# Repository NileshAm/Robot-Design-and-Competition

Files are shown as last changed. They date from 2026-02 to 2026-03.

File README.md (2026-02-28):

# Robot Design and Competition
This is the project repository for module EN2533-Robot Design and Competition.</br>
This repository contains all the [design](/Design/) files and [firmware](/Code/) for for the robot we designed.

## Final product

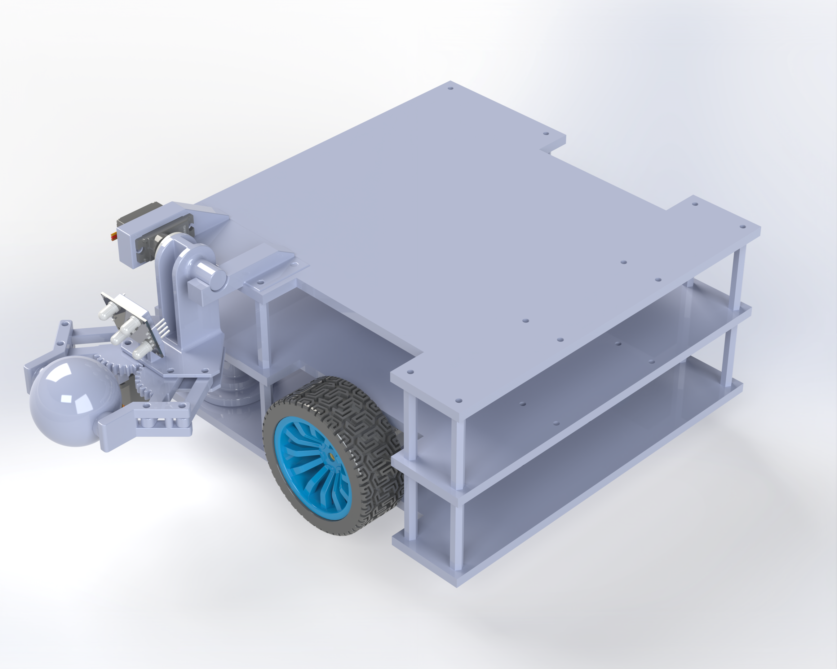
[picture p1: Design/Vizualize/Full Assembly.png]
Robot Image


<p align="center">
  
  
</p>

### Component Selection
| Category | Component | Model / Specification | Quantity | Reason for Selection |
|---|---|---|---|---|
| Controller | Microcontroller | Arduino Mega 2560 | 1 | Mainly choosen for its high pin count to handle the sensors |
| Motor Driver | Motor Driver Module | bts7960 motor driver | 2 | Provides bidirectional control and sufficient current for DC motors |
| Actuator | JGA25-370 12V with encoders | 12V, 280 RPM | 2 | High torque suitable and encoder for precision control of the  robot |
| Battery | 11.1V LiPo |  4800mah | 1 | Lightweight with high energy density |
| Power Regulation | Voltage Regulator | Buck Converter (LM2596),  | 2 | Steps down battery voltage safely for electronics (2 is used for a electronics rail and a high power rail seperated for electronics stability.) |
| Power Regulation | Voltage Regulator | 12V Buck Boost converter,  | 1 | To regulate the motor voltage to be at constant 12V. |
| Sensor | Distance Sensor | VL53LOX Tof Sensors | 5 | Obstacle detection |
| Sensor | Line Sensor | IR Reflective Sensor | 8 | Line-following capability |
| Mechanical | Chassis | 3D Printed | 1 | Strong, lightweight, and custom-fit |
| Mechanical | Wheel | Rubber Wheel (65 mm) | 4 | Good traction and stability |
| Interface | Display | OLED | 1 | System status and debugging feedback |
| Safety | Switch | Toggle / Push Button | 1 | Safe power isolation |

## Folder structure

- [Design](/Design/) : Contains all the robot design files
  - [Parts](/Design/Parts/) : Contains all part files of the design.
  - [Assemblies](/Design/Assemblies/) : Contains all the assembly files.
  - [Drawings](/Design/Drawings/) : Contains all the enginnering drawing files.
  - [Manufacturing](/Design/Manufacturing/) : Contains all the files required to manufacture the robot.

- [Code](/Code/) : Contains all the firmware for the robot.
  - [include](/Code/include/) : Project headers for files. ([/include/README.md](/Code/include/README.md))
  - [lib](/Code/lib/) : Project specific component files. ([/lib/README.md](/Code/lib/README.md))
  - [src](/Code/src/) : Main file of the project.
  - [test](/Code/test/) : Test files of the project. ([/test/README.md](/Code/test/README.md))

## Branching Structure

- **Main Branch** : All the design and firmware files.
- **Design branch** : Changes made to the design of the robot is done here
  - **Design sub-branch** : Individual changes of the desgin of the robot are done in these braches.<br>
    - Name must follow the convention : `design-*`<br>
      - Example : `design-arm`

    - After finishing the sub-branch design, branch must be merged with the **Design branch** with and the with the **Main branch**.
  - **Code sub-branch** : Individual changes of firmware of the robot are done in these braches.<br>
    - Name must follow the convention : `code-*`<br>
      - Example : `code-PID`

    - After finishing the sub-branch, branch must be merged with the **Code branch** with and the with the **Main branch**.

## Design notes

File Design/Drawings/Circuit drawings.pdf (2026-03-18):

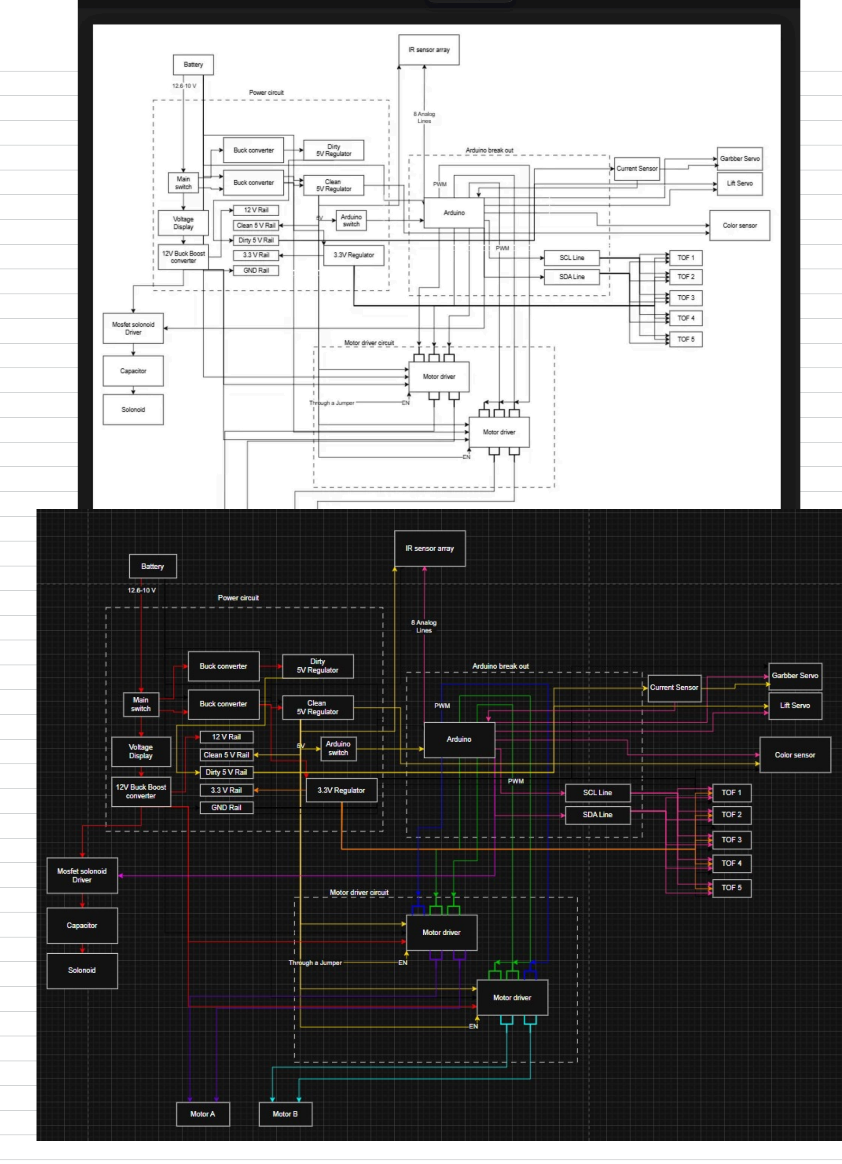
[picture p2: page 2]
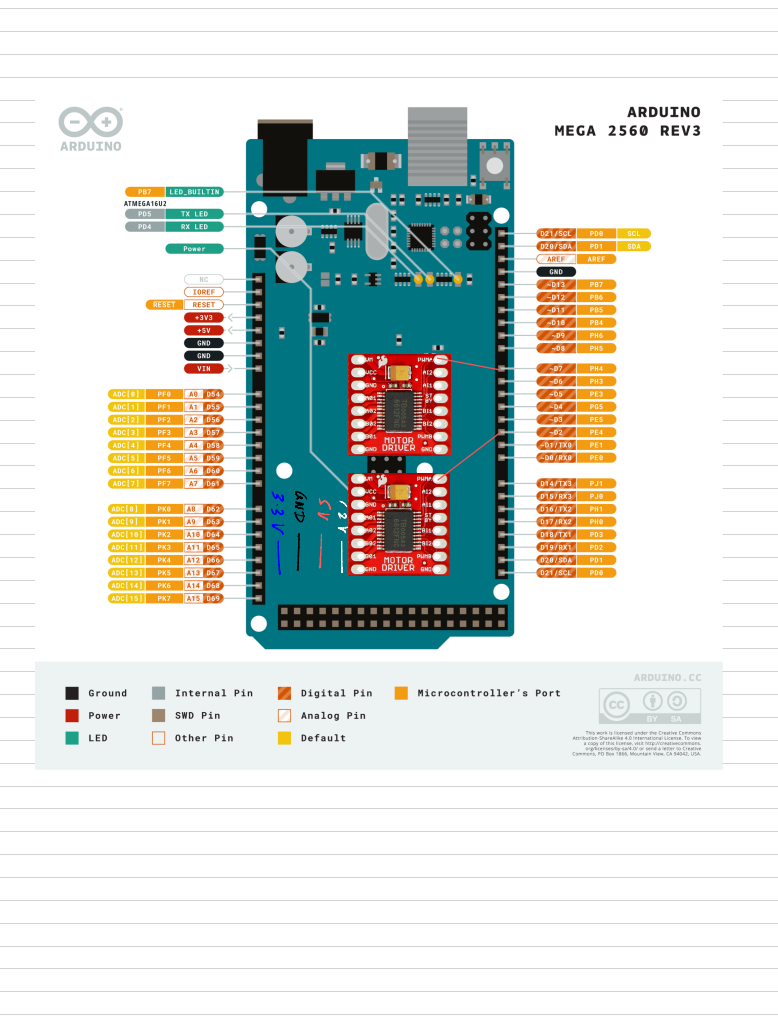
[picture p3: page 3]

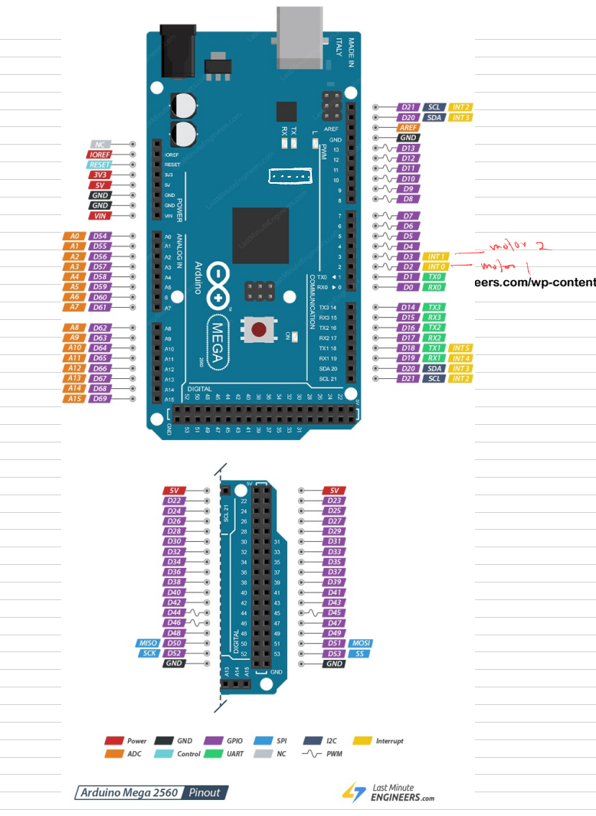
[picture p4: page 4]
motor 2; motor (

https://lastminuteengineers.com/wp-content/uploads/arduino/Arduino-Mega-2560-Pinout.png

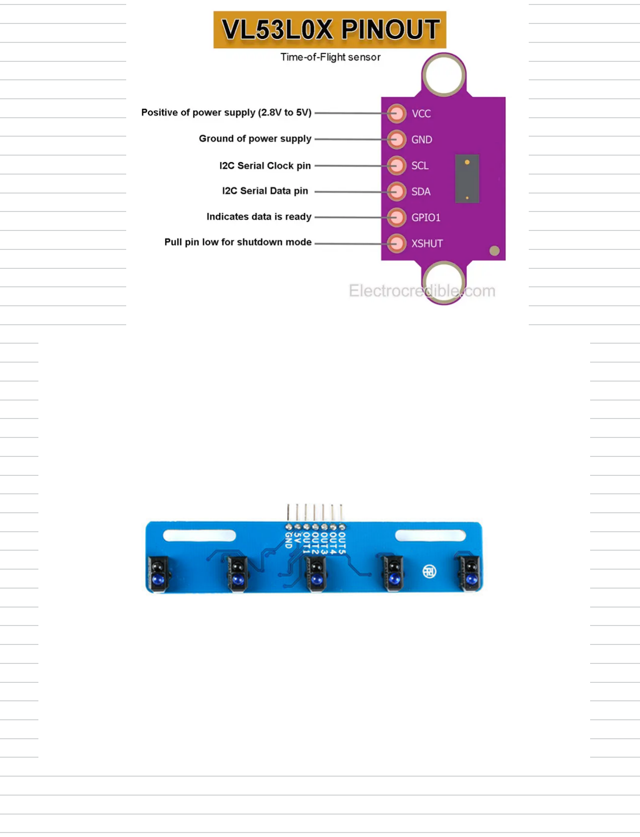
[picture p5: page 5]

https://www.google.com/url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

https://content.instructables.com/FCN/O9VG/JHATTMWR/FCNO9VGJHATTMWR.png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.

https://www.google.com/url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

# aut

↳

motor powere

,

⑧ | -S

2

C

# motor power

# =>inteaua digital

E

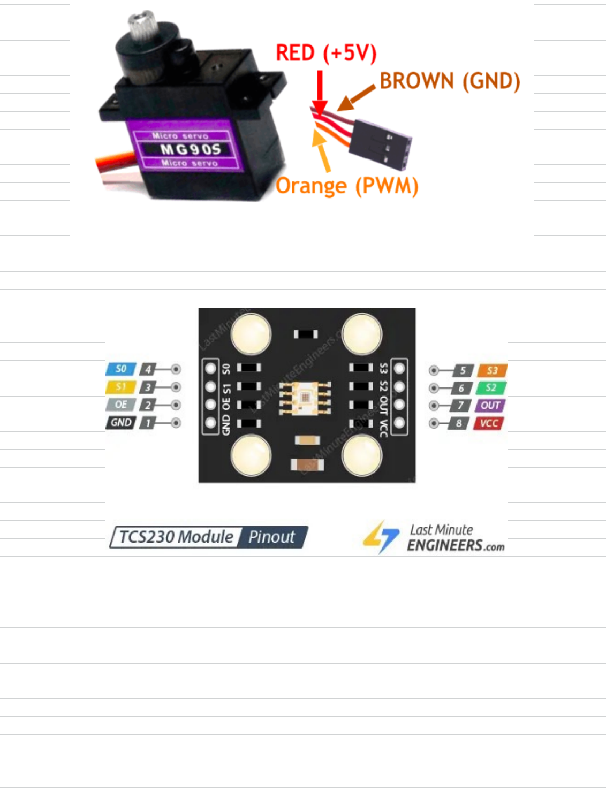
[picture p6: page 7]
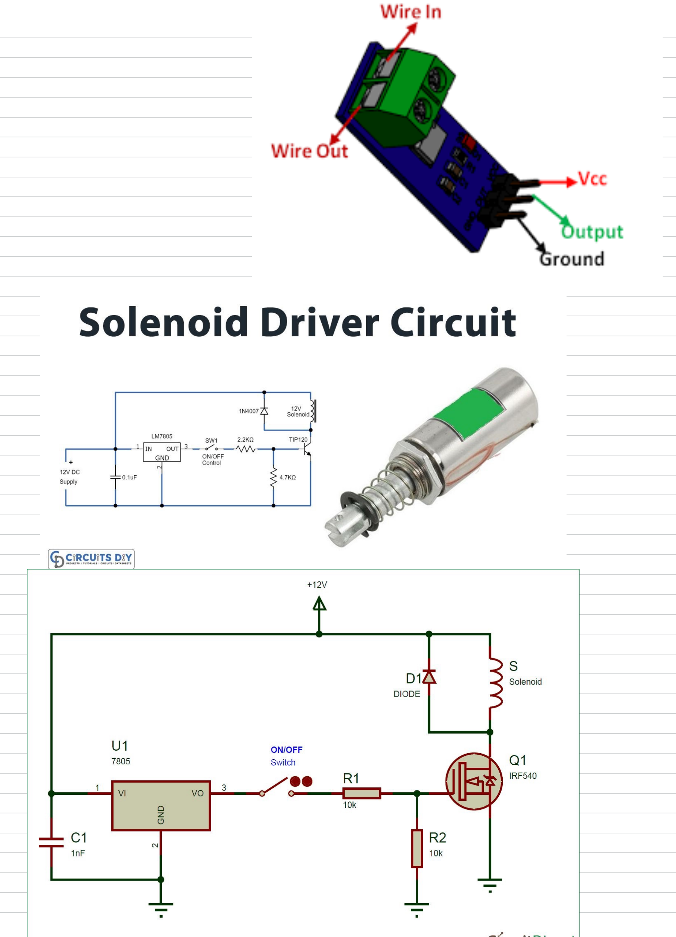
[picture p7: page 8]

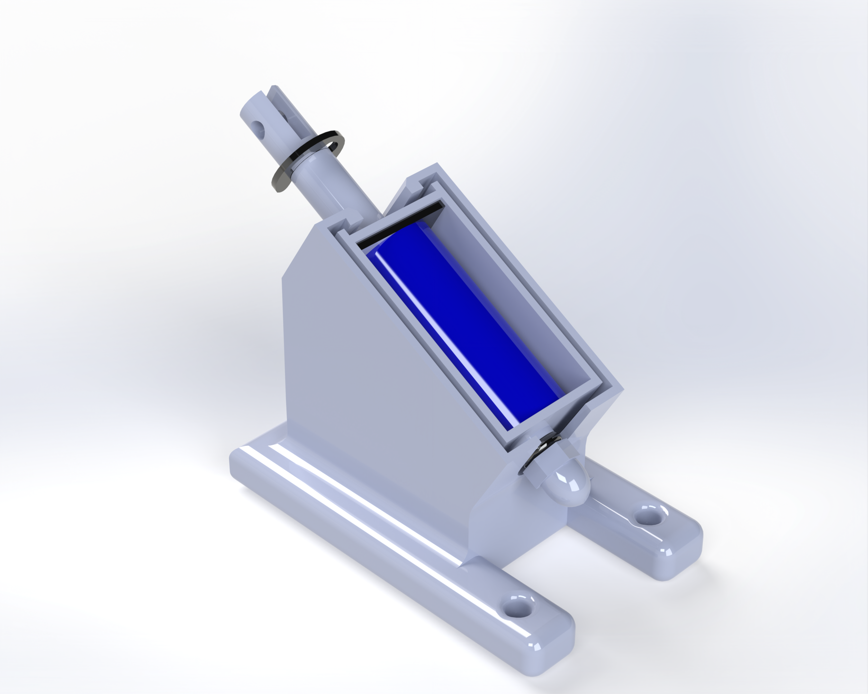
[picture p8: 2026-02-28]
Design/Vizualize/Solenoid.png

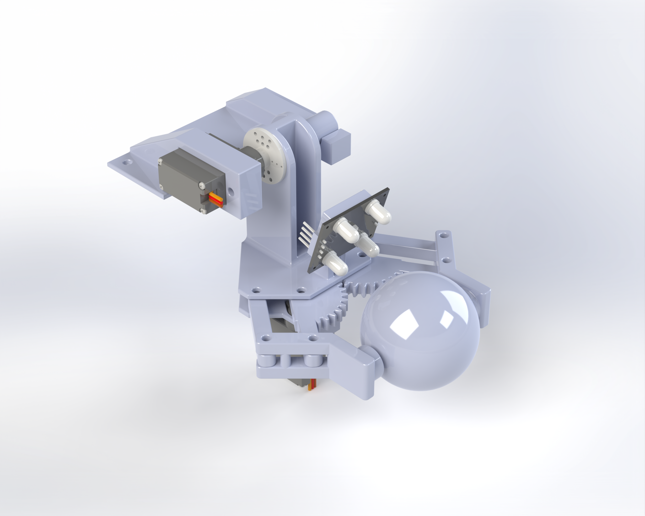
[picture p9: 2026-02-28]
Design/Vizualize/Grabber.png

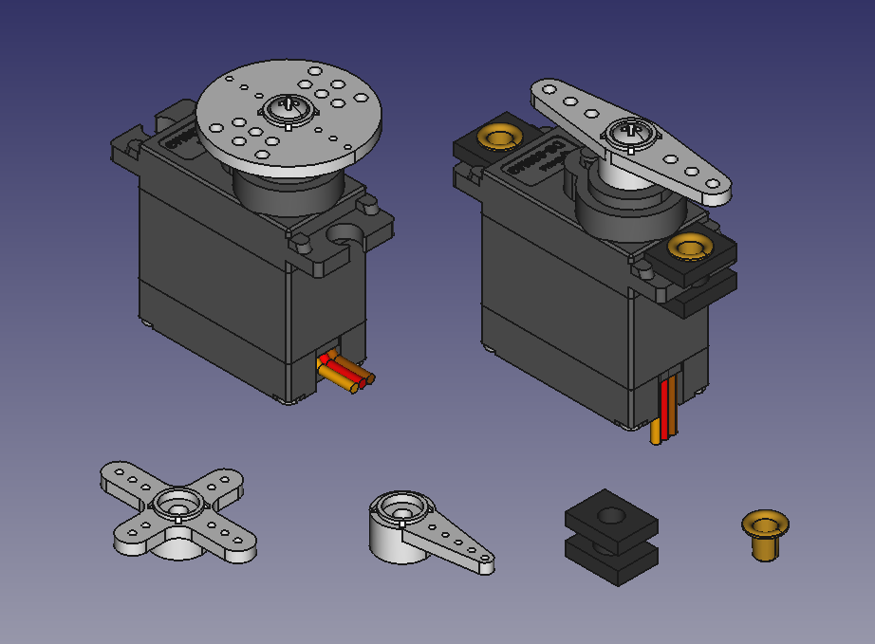
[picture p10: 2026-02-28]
Design/Downloads/digital-servo-corona-ds-939mg-with-accessories-1.snapshot.11/Corona_DS939MG_Set.png

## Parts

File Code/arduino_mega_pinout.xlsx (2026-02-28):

Pin_Name | Pin_Number | Type | PWM | UART | I2C | SPI | Interrupt | Onboard_Feature | Usage Type | Usage
D0 | 0 | Digital I/O | No | RX0 (Serial0) |  |  | No
D1 | 1 | Digital I/O | No | TX0 (Serial0) |  |  | No
D2 | 2 | Digital I/O | Yes |  |  |  | Yes |  | Right Motor | encA
D3 | 3 | Digital I/O | Yes |  |  |  | Yes |  | Left Motor | encA
D4 | 4 | Digital I/O | Yes |  |  |  | No |  | Right Motor | PWM backward
D5 | 5 | Digital I/O | Yes |  |  |  | No |  | Right Motor | PWM forward
D6 | 6 | Digital I/O | Yes |  |  |  | No |  | Right Motor | PWM forward
D7 | 7 | Digital I/O | Yes |  |  |  | No |  | Right Motor | PWM backward
D8 | 8 | Digital I/O | Yes |  |  |  | No |  | Servo | Grabber
D9 | 9 | Digital I/O | Yes |  |  |  | No |  | Servo | Lift
D10 | 10 | Digital I/O | Yes |  |  |  | No
D11 | 11 | Digital I/O | Yes |  |  |  | No
D12 | 12 | Digital I/O | Yes |  |  |  | No
D13 | 13 | Digital I/O | Yes |  |  |  | No | On-board LED (L)
D14 | 14 | Digital I/O | No | TX3 (Serial3) |  |  | No
D15 | 15 | Digital I/O | No | RX3 (Serial3) |  |  | No
D16 | 16 | Digital I/O | No | TX2 (Serial2) |  |  | No
D17 | 17 | Digital I/O | No | RX2 (Serial2) |  |  | No
D18 | 18 | Digital I/O | No | TX1 (Serial1) |  |  | Yes
D19 | 19 | Digital I/O | No | RX1 (Serial1) |  |  | Yes
D20 | 20 | Digital I/O | No |  | SDA (I2C) |  | Yes |  | I2C | SDA
D21 | 21 | Digital I/O | No |  | SCL (I2C) |  | Yes |  | I2C | SCL
D22 | 22 | Digital I/O | No |  |  |  | No |  | Right Motor | encB
D23 | 23 | Digital I/O | No |  |  |  | No |  | IR | IR
D24 | 24 | Digital I/O | No |  |  |  | No |  | Left Motor | encB
D25 | 25 | Digital I/O | No |  |  |  | No |  | IR | IR
D26 | 26 | Digital I/O | No |  |  |  | No
D27 | 27 | Digital I/O | No |  |  |  | No |  | IR | IR
D28 | 28 | Digital I/O | No |  |  |  | No |  | Right Motor | dir1
D29 | 29 | Digital I/O | No |  |  |  | No |  | IR | IR
D30 | 30 | Digital I/O | No |  |  |  | No |  | Right Motor | dir2
D31 | 31 | Digital I/O | No |  |  |  | No |  | IR | IR
D32 | 32 | Digital I/O | No |  |  |  | No |  | Left Motor | dir1
D33 | 33 | Digital I/O | No |  |  |  | No |  | IR | IR
D34 | 34 | Digital I/O | No |  |  |  | No |  | Left Motor | dir2
D35 | 35 | Digital I/O | No |  |  |  | No |  | IR | IR
D36 | 36 | Digital I/O | No |  |  |  | No |  | Tof | Right Tof
D37 | 37 | Digital I/O | No |  |  |  | No |  | IR | IR
D38 | 38 | Digital I/O | No |  |  |  | No |  | Tof | Front Top Tof
D39 | 39 | Digital I/O | No |  |  |  | No
D40 | 40 | Digital I/O | No |  |  |  | No |  | Tof | Front TOF
D41 | 41 | Digital I/O | No |  |  |  | No
D42 | 42 | Digital I/O | No |  |  |  | No |  | Tof | Left Tof 2
D43 | 43 | Digital I/O | No |  |  |  | No |  | Grabber Color | S0
D44 | 44 | Digital I/O | Yes |  |  |  | No |  | Tof | Left Tof
D45 | 45 | Digital I/O | Yes |  |  |  | No |  | Grabber Color | S1
D46 | 46 | Digital I/O | Yes |  |  |  | No
D47 | 47 | Digital I/O | No |  |  |  | No |  | Grabber Color | S2
D48 | 48 | Digital I/O | No |  |  |  | No |  | Button | Down Button
D49 | 49 | Digital I/O | No |  |  |  | No |  | Grabber Color | S3
D50 | 50 | Digital I/O | No |  |  | MISO (SPI) | No |  | Button | Up Button
D51 | 51 | Digital I/O | No |  |  | MOSI (SPI) | No |  | Grabber Color | out
D52 | 52 | Digital I/O | No |  |  | SCK (SPI) | No |  | Button | Select Button
D53 | 53 | Digital I/O | No |  |  | SS (SPI) | No |  | Grabber Color | OE
A0 | 54 | Analog Input / Digital I/O | No |  |  |  | No |  | Box Color | S0
A1 | 55 | Analog Input / Digital I/O | No |  |  |  | No |  | Box Color | S1
A2 | 56 | Analog Input / Digital I/O | No |  |  |  | No |  | Box Color | S2
A3 | 57 | Analog Input / Digital I/O | No |  |  |  | No |  | Box Color | S3
A4 | 58 | Analog Input / Digital I/O | No |  |  |  | No |  | Box Color | out
A5 | 59 | Analog Input / Digital I/O | No |  |  |  | No |  | Box Color | OE
A6 | 60 | Analog Input / Digital I/O | No |  |  |  | No
A7 | 61 | Analog Input / Digital I/O | No |  |  |  | No
A8 | 62 | Analog Input / Digital I/O | No |  |  |  | No |  | Currect sensor | Currect sensor
A9 | 63 | Analog Input / Digital I/O | No |  |  |  | No
A10 | 64 | Analog Input / Digital I/O | No |  |  |  | No
A11 | 65 | Analog Input / Digital I/O | No |  |  |  | No
A12 | 66 | Analog Input / Digital I/O | No |  |  |  | No
A13 | 67 | Analog Input / Digital I/O | No |  |  |  | No
A14 | 68 | Analog Input / Digital I/O | No |  |  |  | No
A15 | 69 | Analog Input / Digital I/O | No |  |  |  | No
IOREF |  | Power/Ref
RESET |  | Reset
3.3V |  | Power
5V |  | Power
GND |  | Ground
GND |  | Ground
VIN |  | Power Input
AREF |  | Analog Reference
GND |  | Ground
GND |  | Ground
SDA | 20 | I2C Header |  |  | SDA (I2C, same as D20)
SCL | 21 | I2C Header |  |  | SCL (I2C, same as D21)
ICSP_MISO | 50 | SPI (ICSP) |  |  |  | MISO (SPI, same as D50)
ICSP_MOSI | 51 | SPI (ICSP) |  |  |  | MOSI (SPI, same as D51)
ICSP_SCK | 52 | SPI (ICSP) |  |  |  | SCK (SPI, same as D52)
ICSP_RESET |  | Reset (ICSP)
ICSP_VCC |  | Power (ICSP)
ICSP_GND |  | Ground (ICSP)

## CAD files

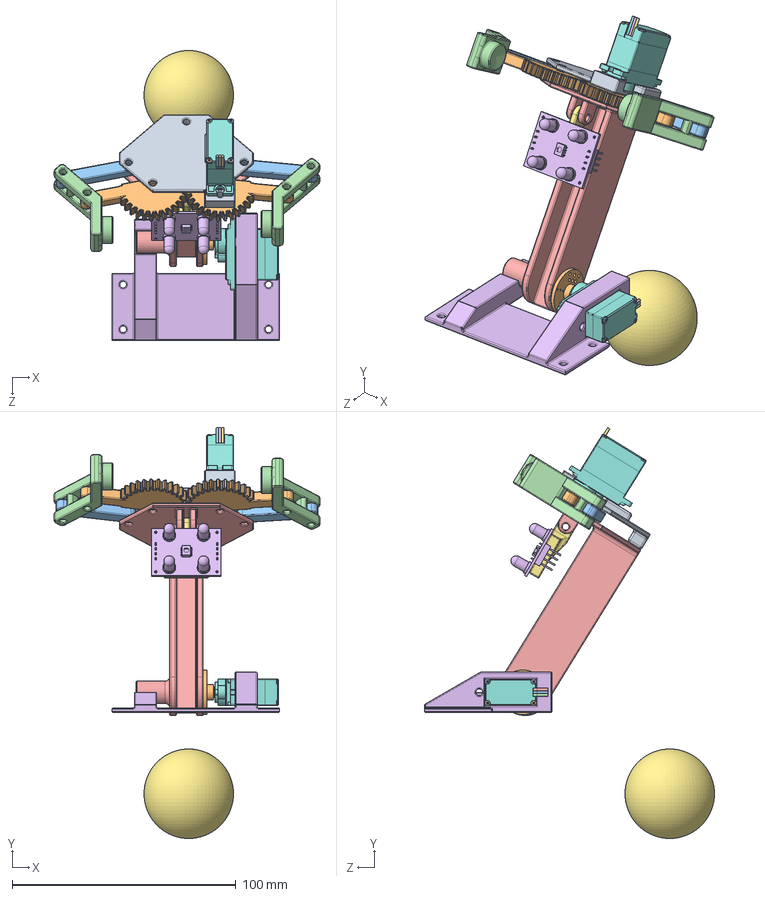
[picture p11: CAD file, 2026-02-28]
Design/Assemblies/Grabber.SLDASM
118.7 x 183.7 x 129.6 mm
Grabber base bottom
Link front x 2
Link back x 2
Grabbing link x 2
Grabber base top
TCS230-TCS3200
Color sensor mount
Corps.step x 2
M1.2-Screw001.step x 2
M1.2-Screw002.step x 2
M1.2-Screw003.step x 2
M1.2-Screw004.step x 2
Axe.step x 2
FilRougeDroit.step
FilMarronDroit.step
FilOraqngeDroit.step
Etiquette2.step x 2
Corona_DS939MG-BrasRond.step
FilRougeCoude.step
FilMarronCoude001.step
FilOrangeCoude002.step
Lift servo mount
Ball

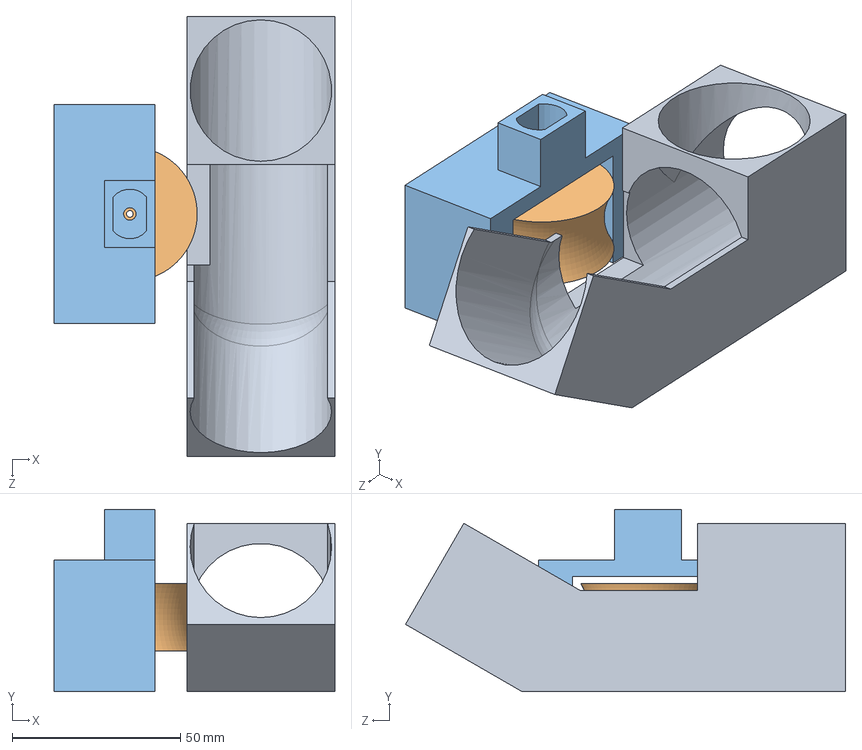
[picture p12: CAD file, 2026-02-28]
Design/Assemblies/Shooter.SLDASM
83.4 x 54.1 x 130.6 mm
Ramp
Fly wheel
Fly wheel motor mount

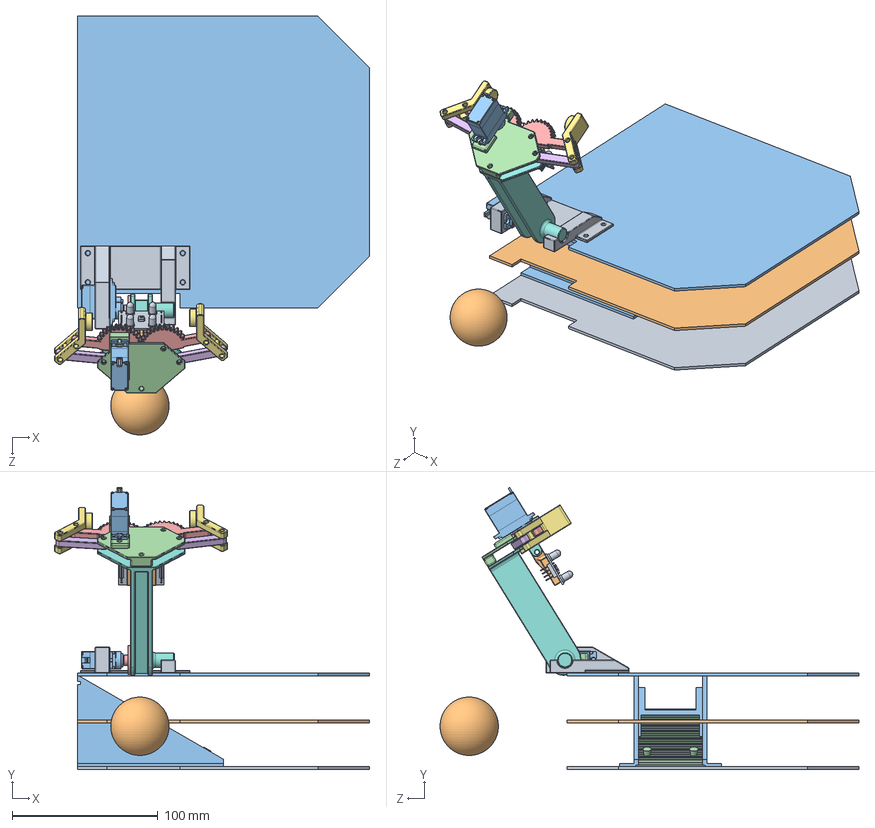
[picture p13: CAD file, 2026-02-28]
Design/Assemblies/Robot.SLDASM
215.9 x 193.3 x 287.1 mm
Base level
Level 2
Level 3
Grabber base bottom
Link front x 2
Link back x 2
Grabbing link x 2
Grabber base top
TCS230-TCS3200
Color sensor mount
Corps.step x 2
M1.2-Screw001.step x 2
M1.2-Screw002.step x 2
M1.2-Screw003.step x 2
M1.2-Screw004.step x 2
Axe.step x 2
FilRougeDroit.step
FilMarronDroit.step
FilOraqngeDroit.step
Etiquette2.step x 2
Corona_DS939MG-BrasRond.step
FilRougeCoude.step
FilMarronCoude001.step
FilOrangeCoude002.step
Lift servo mount
Ball
Slider base
Rack

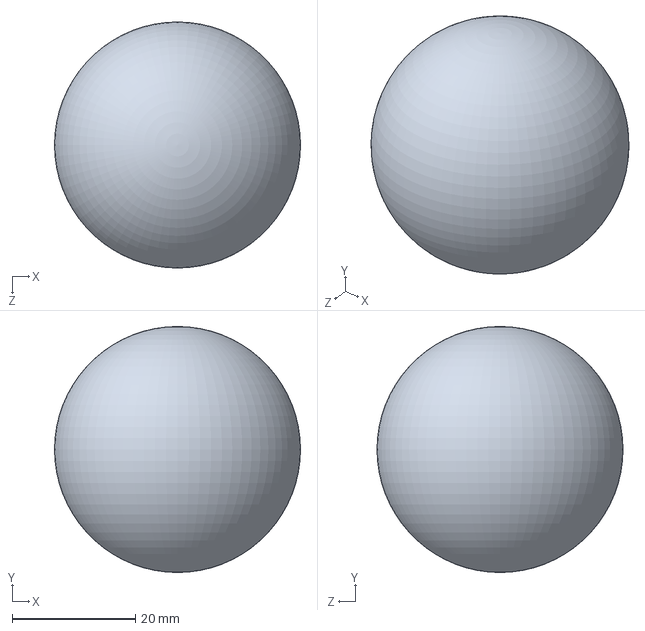
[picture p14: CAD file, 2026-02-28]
Design/Arena/Ball.SLDPRT
40.0 x 40.0 x 40.0 mm

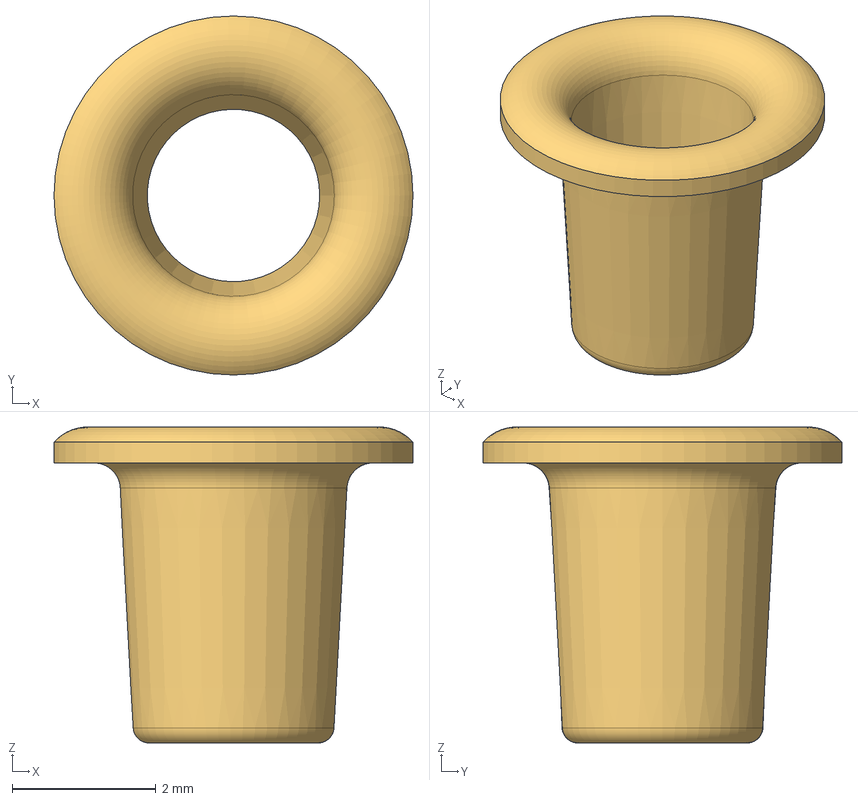
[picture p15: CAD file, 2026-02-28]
Design/Downloads/digital-servo-corona-ds-939mg-with-accessories-1.snapshot.11/Corona_DS939MG_Accessoires.FCStd
5.00 x 5.00 x 4.40 mm

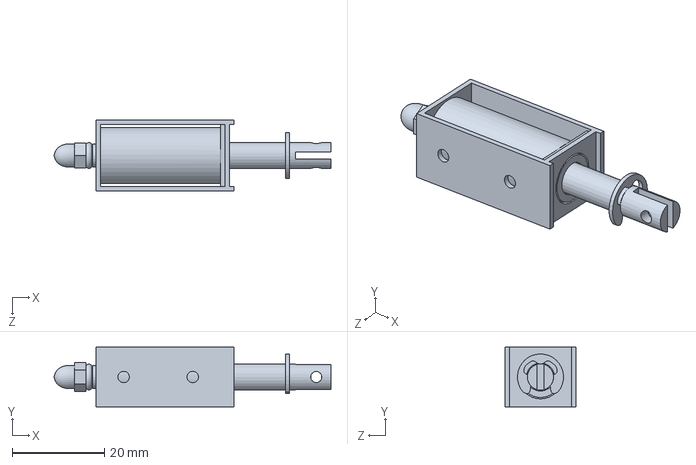
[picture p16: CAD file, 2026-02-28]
Design/Downloads/JF-0530B Selenoid itme çekme valfi.SLDPRT
60.1 x 13.0 x 15.5 mm

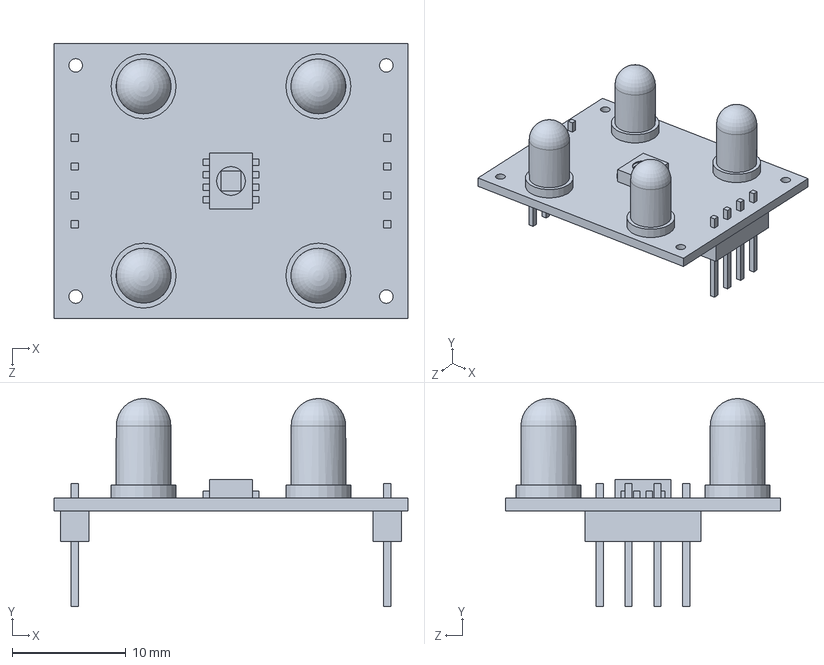
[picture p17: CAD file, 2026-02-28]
Design/Downloads/tcs230-tcs3200-1.snapshot.1/TCS230-TCS3200.SLDPRT
31.1 x 18.3 x 24.1 mm

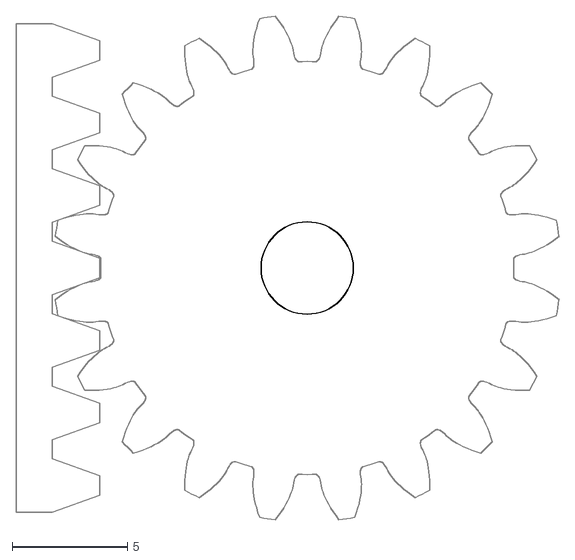
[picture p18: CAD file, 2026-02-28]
Design/Gears/Rack and pinion.dxf
23.5 x 21.8

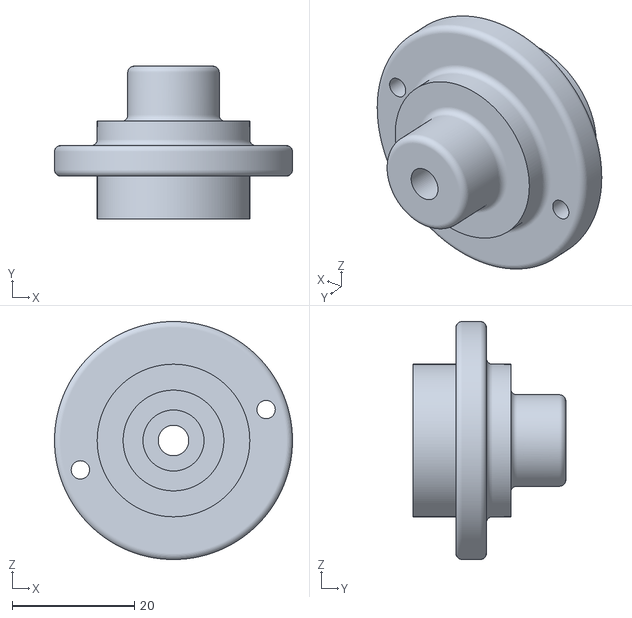
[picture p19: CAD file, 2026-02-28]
Design/Manufacturing/Ball Bearim 3_V0.2.STL
39.0 x 25.0 x 39.0

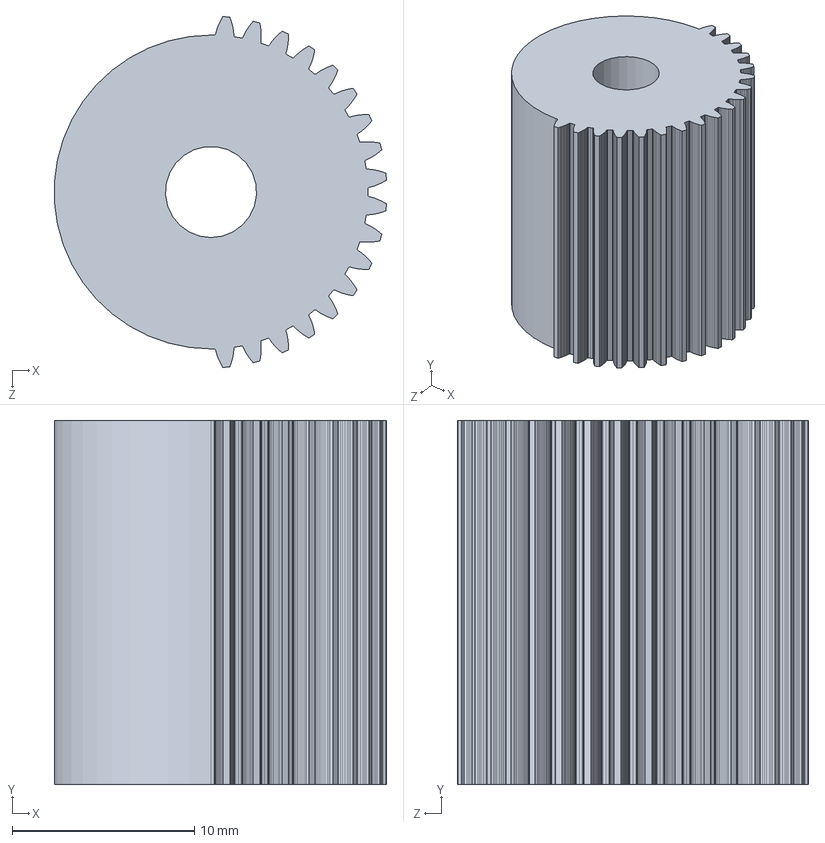
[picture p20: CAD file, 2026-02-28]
Design/Parts/Gear_new_1.SLDPRT
18.2 x 20.0 x 19.3 mm

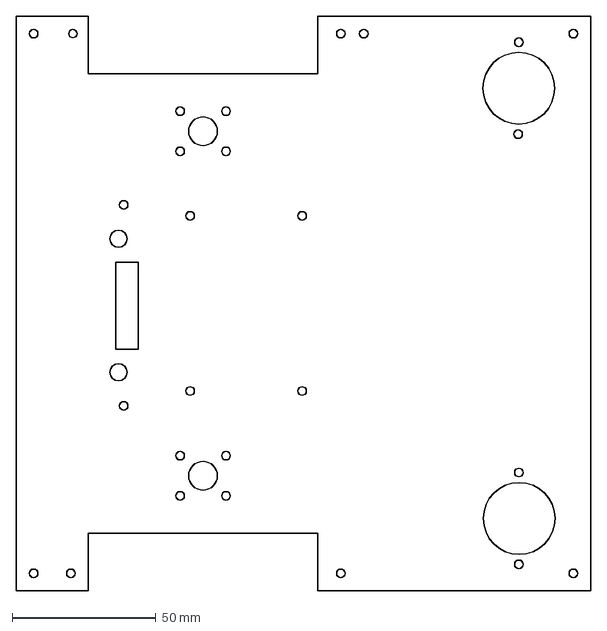
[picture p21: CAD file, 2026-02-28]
Design/Drawings/Chasis 01_V0.3.DXF
200.0 x 200.0 mm

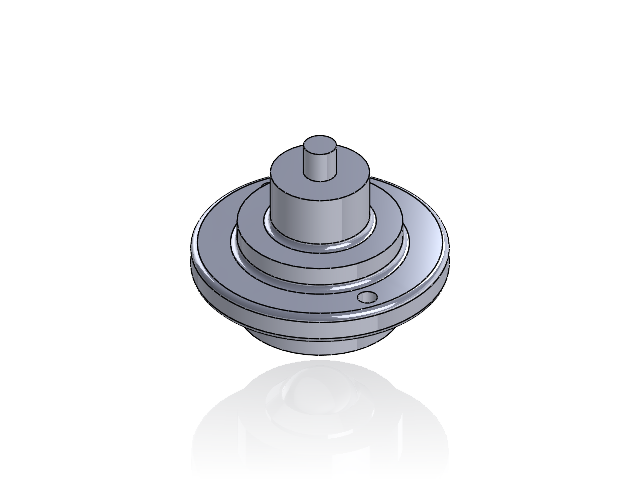
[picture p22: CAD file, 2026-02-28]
Assmblies/Ball Bearim_Assembly_with_mount.SLDASM
Ball Bearim 1
Ball Bearim 2
Ball Bearim 3_V0.2

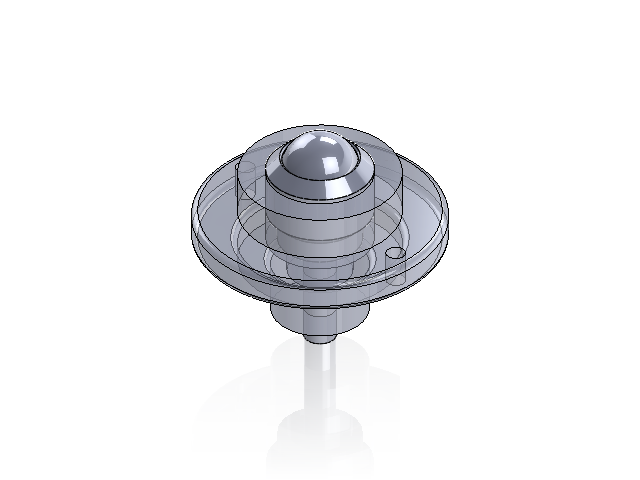
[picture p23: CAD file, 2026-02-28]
Assmblies/Ball Bearim.SLDASM
Ball Bearim 1
Ball Bearim 2
Ball Bearim 3_V0.2

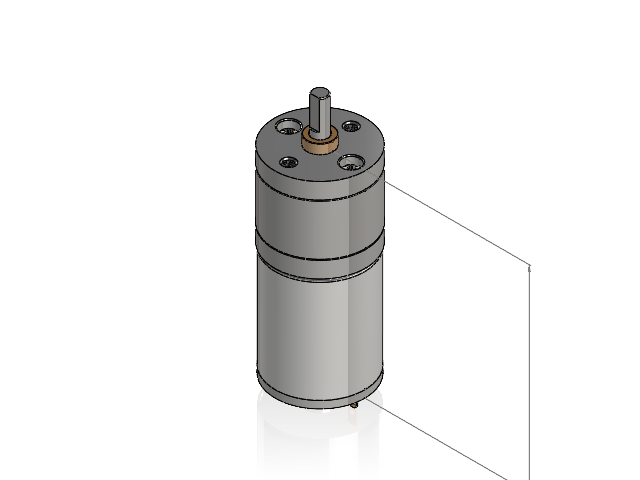
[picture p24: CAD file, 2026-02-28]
Design/Downloads/JGA25-370.SLDASM
Motor.step
Gearbox.step
90116A027_316 Stainless Steel Pan Head Phillips Screws.step x 2

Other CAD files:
Assmblies/IE ARRAY.SLDASM
Assmblies/Solenoid_Assembly.SLDASM
Assmblies/Shooter_Assembly_V0.2.SLDASM
Design/Downloads/digital-servo-corona-ds-939mg-with-accessories-1.snapshot.11/Corona_DS939MG_Fixing.step
Design/Downloads/SG90-servo.SLDPRT
Design/Downloads/digital-servo-corona-ds-939mg-with-accessories-1.snapshot.11/Corona_DS939MG-BrasCroix.step
Design/Downloads/digital-servo-corona-ds-939mg-with-accessories-1.snapshot.11/Corona_DS939MG-BrasDouble.step
Design/Downloads/digital-servo-corona-ds-939mg-with-accessories-1.snapshot.11/Corona_DS939MG-BrasRond.step
Design/Downloads/digital-servo-corona-ds-939mg-with-accessories-1.snapshot.11/Corona_DS939MG-BrasSimple.step
Design/Downloads/digital-servo-corona-ds-939mg-with-accessories-1.snapshot.11/Corona_DS939MG_ShockAbsorber.step
Design/Downloads/mounting_motor.SLDPRT
Design/Drawings/Chasis 01_V0.1.DXF
Design/Drawings/Chasis 02_V0.2.DXF
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

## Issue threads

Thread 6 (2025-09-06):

Color sensor helper

NileshAm, 2025-09-06:
### Make a color sensor helper library
- Library file must be made using a **class**. Refer [PID](https://github.com/NileshAm/Robot-Design-and-Competition/tree/code-init/Code/lib/PID) for example of an implemented code.

- [ ] Make the ColorSensor.h file
- [ ] Make the ColorSensor.cpp file
- [ ] Make examples.cpp file in `/examples` folder and write a basic implementation sketch.
- [ ] Implement `isRed()`, `isBlue()`, `isGreen()` , `isBlack()`, `isWhite()` methods.
- [ ] Implement `calibrate()` method.

NileshAm, 2025-09-24:
Completed with 18c24d7ac931fc67b3842cd5ee2de3503973ed4a commit.

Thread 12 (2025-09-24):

User menu

NileshAm, 2025-09-24:
## Menu implementation
Implementing the menu that controls the robot.

Implementation strategy for the menu is **_not finalized_**.

- [ ] Implement a menu that shows the items. Menu should be as follows.
```python
* Run All  // * marks the current selection
  Calibrate
  Run task 1
  .
  .
  .
```

- [ ] 2 buttons must be configured to go up and down the menu.
- [ ] 1 interrupt button must be configured.
  - To stop the current task if a task is running and open the menu.
  - To select the selected(the menu item where the `*` is current located)
- [ ] Apon selection method should return a value (Preferably a `int`), to be used in a switch case to put the robot in each state.

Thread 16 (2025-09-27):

Grabber helper

NileshAm, 2025-09-27:
## Grabber helper

Features to be implemented

- [ ] `Grabber` class with constructor.
- [ ] constructor must take 2 servo motors, current sensor and grabber tof as parameters and initialize them.
- [ ] `grab` method must turn the servo till current spike is detected and grab the object.
- [ ] `lift` method must lift the arm from initial position to the release position.
- [ ] `relaese` method must open the grabbers fully.
- [ ] `reset` method must bring down the arm and make the grabber ready to grab the next object.

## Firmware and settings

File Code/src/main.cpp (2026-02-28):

#include <Arduino.h>
#include <Motor.h>
#include <IRArray.h>
#include <Tof.h>
#include <OLED.h>
#include <ColorSensor.h>
#include <Grabber.h>
#include <ServoMotor.h>
#include <CurrentSensor.h>
#include <Robot.h>
#include <Utils.h>
#include <pushbutton.h>
#include <MenuSystem.h>
#include <UpdatePID.h>
#include <ServoMotor.h>
#include <MPU6050.h>

void setup()
{
    Serial.begin(9600);
    Serial.println("Setup started...");
    

    OLED oled;
    oled.begin();
    oled.displayText("Initializing...", 0, 0, 1);
    Serial.println("Initializing...");

    Motor leftMotor(28, 30, 4, 5, 2, 22, 450); // dir1, dir2, pwmF, pwmB, encA, encB, ticks/rev     motor controller 1
    Motor rightMotor(32, 34, 7, 6, 3, 24, 450);  // dir1, dir2, pwmF, pwmB, encA, encB, ticks/rev   motor controller 2
    leftMotor.init();
    rightMotor.init();
    oled.displayText("Motor init complete...", 0, 10, 1);
    
    const uint8_t PINS[8] = {23, 25, 27, 29, 31, 33, 35, 37};
    // equal weights (or set your own)
    const float W[8] = {0, 100, 200, 300, 400, 500, 600, 700};
    IRArray ir(8, PINS, W, 0.5f);
    ir.init();
    oled.displayText("IR init complete...", 0, 20, 1);

    Tof frontTof(40, 0x30, 20, 21);    // xshut, address, sda, scl
    Tof leftTof(44, 0x31, 20, 21);     // xshut, address, sda, scl
    Tof leftTof2(42, 0x34, 20, 21);    // xshut, address, sda, scl
    Tof rightTof(36, 0x32, 20, 21);    // xshut, address, sda, scl
    Tof frontTopTof(38, 0x33, 20, 21); // xshut, address, sda, scl

    frontTof.disable();
    leftTof.disable();
    leftTof2.disable();
    rightTof.disable();
    frontTopTof.disable();

    frontTof.init(25);
    leftTof.init(20);
    leftTof2.init(-8);
    rightTof.init(17);
    frontTopTof.init(48);

    ColorSensor boxColorSensor(A0, A1, A2, A3, A4, A5);
    ColorSensor grabberSensor(43, 45, 47, 49, 51, 53);
    boxColorSensor.begin();
    grabberSensor.begin();
    oled.displayText("Color init complete...", 0, 40, 1);
    
    pushbutton btnUp(50);
    pushbutton btnDown(48);
    pushbutton btnSelect(52);
    btnUp.init();
    btnDown.init();
    btnSelect.init();
    oled.clear();
    oled.displayText("Button init complete...", 0, 0, 1); 
    
    // --- Grabber Initialization ---
    ServoMotor grabServo(8); 
    ServoMotor liftServo(9);
    CurrentSensor currentSensor(A8, 0.001, 60); 
    Grabber grabber(grabServo, liftServo, currentSensor);
    grabber.init();
    
    MPU6050 imu = MPU6050();
    imu.begin();
    oled.displayText("IMU init complete...", 0, 10, 1);

    Robot robot(rightMotor, leftMotor, ir, frontTof, leftTof, leftTof2, frontTopTof, rightTof, grabberSensor, boxColorSensor, grabber, oled, imu);
    oled.displayText("Robot init complete...", 0, 10, 1);


    oled.clear();
    MenuSystem *menu;
    menu = new MenuSystem(oled, btnUp, btnDown, btnSelect, grabberSensor, robot);

    // Initialize Menu
    menu->begin();
    while (true)
    {
        menu->update();
        delay(10);
    }

}

void loop()
{
    // Empty because we have a while(true) in setup,
    // but typically we should move the while(true) content here.
    // For now, keeping it in setup to match existing style,
    // but the while(true) above handles the loop.
}

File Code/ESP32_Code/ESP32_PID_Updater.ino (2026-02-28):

#include <WiFi.h>
#include <WebServer.h>
#include <Preferences.h>

// ---- CONFIGURATION ----
const char* ssid = "Robot_PID_Tuner";  // AP Name
const char* password = "password123";  // AP Password

// Pin connected to Arduino RESET pin
#define ARDUINO_RESET_PIN 4 

// UART to Arduino (Serial2)
#define RXD2 16
#define TXD2 17

Preferences preferences;
WebServer server(80);

// PID Values Structure
struct PIDValues {
  float kp;
  float ki;
  float kd;
};

PIDValues linePID = {0.25, 0.0, 70.0};
PIDValues wallPID = {0.25, 0.1, 90.0};
PIDValues straightPID = {1.5, 1.0, -0.25};

// HTML Page
void handleRoot() {
  String html = R"rawliteral(
<!DOCTYPE HTML><html>
<head>
  <title>PID Tuner</title>
  <meta name="viewport" content="width=device-width, initial-scale=1">
  <style>
    body { font-family: Arial; text-align: center; margin: 0px auto; padding-top: 30px; }
    input, select { padding: 10px; font-size: 20px; width: 80%; max-width: 300px; margin: 10px; }
    input[type=submit] { background-color: #4CAF50; border: none; color: white; padding: 16px 32px; text-decoration: none; margin: 4px 2px; cursor: pointer; font-size: 20px;}
    .label { display: inline-block; width: 50px; text-align: right; font-weight: bold; }
  </style>
  <script>
    var pids = {
      0: { kp: )rawliteral" + String(linePID.kp) + R"rawliteral(, ki: )rawliteral" + String(linePID.ki) + R"rawliteral(, kd: )rawliteral" + String(linePID.kd) + R"rawliteral( },
      1: { kp: )rawliteral" + String(wallPID.kp) + R"rawliteral(, ki: )rawliteral" + String(wallPID.ki) + R"rawliteral(, kd: )rawliteral" + String(wallPID.kd) + R"rawliteral( },
      2: { kp: )rawliteral" + String(straightPID.kp) + R"rawliteral(, ki: )rawliteral" + String(straightPID.ki) + R"rawliteral(, kd: )rawliteral" + String(straightPID.kd) + R"rawliteral( }
    };

    function updateFields() {
      var type = document.getElementById("pidType").value;
      document.getElementById("kp").value = pids[type].kp;
      document.getElementById("ki").value = pids[type].ki;
      document.getElementById("kd").value = pids[type].kd;
    }
  </script>
</head>
<body onload="updateFields()">
  <h2>Robot PID Tuner</h2>
  <form action="/update" method="POST">
    <select id="pidType" name="type" onchange="updateFields()">
      <option value="0">Line Follower</option>
      <option value="1">Wall Follower</option>
      <option value="2">Straight Line</option>
    </select><br>
    
    <span class="label">Kp:</span> <input type="text" id="kp" name="kp"><br>
    <span class="label">Ki:</span> <input type="text" id="ki" name="ki"><br>
    <span class="label">Kd:</span> <input type="text" id="kd" name="kd"><br>
    
    <input type="submit" value="Update Robot">
  </form>
</body>
</html>
)rawliteral";
  server.send(200, "text/html", html);
}

void handleUpdate() {
  if (!server.hasArg("type") || !server.hasArg("kp") || !server.hasArg("ki") || !server.hasArg("kd")) {
    server.send(400, "text/plain", "Missing arguments");
    return;
  }

  int type = server.arg("type").toInt();
  float kp = server.arg("kp").toFloat();
  float ki = server.arg("ki").toFloat();
  float kd = server.arg("kd").toFloat();

  // Save to Preferences and update global struct
  preferences.begin("pid", false);
  if (type == 0) {
    preferences.putFloat("l_kp", kp); preferences.putFloat("l_ki", ki); preferences.putFloat("l_kd", kd);
    linePID = {kp, ki, kd};
  } else if (type == 1) {
    preferences.putFloat("w_kp", kp); preferences.putFloat("w_ki", ki); preferences.putFloat("w_kd", kd);
    wallPID = {kp, ki, kd};
  } else if (type == 2) {
    preferences.putFloat("s_kp", kp); preferences.putFloat("s_ki", ki); preferences.putFloat("s_kd", kd);
    straightPID = {kp, ki, kd};
  }
  preferences.end();

  String message = "Type:" + String(type) + ",Kp:" + String(kp) + ",Ki:" + String(ki) + ",Kd:" + String(kd) + "\n";
  
  Serial.println("Received Update: " + message);

  // 1. Reset Arduino
  Serial.println("Resetting Arduino...");
  digitalWrite(ARDUINO_RESET_PIN, LOW);
  delay(100);
  digitalWrite(ARDUINO_RESET_PIN, HIGH);
  
  // 2. Wait for Arduino to boot
  delay(500);

  // 3. Send PID values
  Serial.println("Sending to Arduino: " + message);
  Serial2.print(message);

  server.send(200, "text/html", "<h1>Updated!</h1><p>Values saved and sent to robot.</p><a href=\"/\">Back</a>");
}

void setup() {
  Serial.begin(115200);
  Serial2.begin(9600, SERIAL_8N1, RXD2, TXD2);

  pinMode(ARDUINO_RESET_PIN, OUTPUT);
  digitalWrite(ARDUINO_RESET_PIN, HIGH);

  // Load Preferences
  preferences.begin("pid", true); // Read-only mode first
  linePID.kp = preferences.getFloat("l_kp", linePID.kp);
  linePID.ki = preferences.getFloat("l_ki", linePID.ki);
  linePID.kd = preferences.getFloat("l_kd", linePID.kd);

  wallPID.kp = preferences.getFloat("w_kp", wallPID.kp);
  wallPID.ki = preferences.getFloat("w_ki", wallPID.ki);
  wallPID.kd = preferences.getFloat("w_kd", wallPID.kd);

  straightPID.kp = preferences.getFloat("s_kp", straightPID.kp);
  straightPID.ki = preferences.getFloat("s_ki", straightPID.ki);
  straightPID.kd = preferences.getFloat("s_kd", straightPID.kd);
  preferences.end();

  WiFi.softAP(ssid, password);
  Serial.println("AP Started");
  Serial.print("IP Address: ");
  Serial.println(WiFi.softAPIP());

  server.on("/", handleRoot);
  server.on("/update", handleUpdate);
  server.begin();
  Serial.println("HTTP server started");
}

void loop() {
  server.handleClient();
}

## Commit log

2025-08-27 Migration to Arduino. Migrated from ESP32 (esp-idf) to Arduino (PlatformIO)
2025-08-28 Motor helper made.
2025-08-28 IR Array helper made and utils helper made to print arrays.
2025-08-28 PID helper made
2025-08-31 Servo helper added.
2025-09-01 Straight line PID tuned, Robot functions debuged.
2025-09-01 Dedicated method to print double arrays made.
2025-09-01 Robot IR sensor calibration made. helpers for calibrating while turning is made.
2025-09-01 Wall follower pid rough tune.
2025-09-06 Robot and Motor modified to go till given ticks or given distance.
2025-09-06 Code base initialized and basic functions added. (#1)
    * Migration to Arduino.
    Migrated from ESP32 (esp-idf) to Arduino (PlatformIO)
    * Motor helper made.
    * IR Array helper made and utils helper made to print arrays.
    * PID helper made
    * Tof depandancy imported and helper made.
    * Tof helper debugged.
    * Servo helper added.
    * Robot helper added.
    * Straight line PID tuned, Robot functions debuged.
    * Junction detector made.
    * IRArray modified.
    Made able to set offset and scaling factor.
    * utiles fuhnctions debuged.
    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
    [main.cpp]
2025-09-12 MIgration to PlatformIO and Basic helpers added (#9)
    * Code base initialized and basic functions added. (#1)
    Multiple import error.
    * variable types optimized.
    Types oftimized for better accuracy and lower overhead.
    * Dedicate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
    [main.cpp]
2025-09-12 MIgration to PlatformIO and Basic helpers added (#10)
    * Dedicat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
    [main.cpp]
2025-09-13 Grabber initial design made.
    [Color sensor mount.SLDPRT, Corona_DS939MG-BrasCroix.step, Corona_DS939MG-BrasDouble.step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]
2025-09-13 Some fillets changed, angle constraints added.
    [Color sensor mount.SLDPRT, Grabber base bottom.SLDPRT, Grabber base top.SLDPRT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]
2025-09-15 ultrasonic helper
2025-09-16 Manufacturing files added for grabber.
    [Color sensor mount.STL, Grabber base bottom.SLDPRT, Grabber base bottom.STL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]
2025-09-17 color sensor
2025-09-17 Shooter created.
    [Ball.SLDPRT, Grabber base bottom.SLDPRT, Grabber.SLDASM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]
2025-09-17 Robot assembly made.
    [Base level.SLDPRT, Grabber base bottom.SLDPRT, Grabber base top.SLDPRT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]
2025-09-22 color sensor fixed
2025-09-22 ultrasonic fix
2025-09-27 Robot class updated to hold all sensors.
2025-09-28 Added files upto the V0.3 of the Robo.
    [Ball Bearim 1_V0.2.SLDPRT, Ball Bearim 2_V0.2.SLDPRT, Ball Bearim 3_V0.2.SLDPRT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]
2025-09-28 Added drawings of the new Chasis designs
    [Chasis 01_V0.3.DXF, Chasis 02_V0.3.DXF]
2025-10-10 Add new components: Fly wheel, Fly wheel motor mount, and Ramp
    [Fly wheel motor mount.SLDPRT, Fly wheel.SLDPRT, Ramp.SLDPRT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]
2025-10-15 add grabber and current sensor
2025-11-24 current sensor update
2025-11-26 Add interrupt button functionality to Robot class and integrate into Task1 execution.(AG)
2025-11-26 button up down select works(AG)
2025-11-26 added break buttton..not working(AG)
    [main.cpp]
2025-11-27 Update ServoMotor parameters and enhance Tof initialization logging; modify motor and sensor configurations in main setup
2025-11-27 Fix motor initialization order and enhance moveStraight functionality
    [main.cpp]
2025-11-27 Revert "esp32helper(AG)"
    This reverts commit a9e556773fa6db63926f5ee1cf0a63f97103b21c.
    [main.cpp]
2025-11-27 Implement line following functionality and update calibration process in MenuSystem
2025-11-28 uart communication(AG)
2025-11-28 updated to show current pid values
2025-11-28 Refactor line follower PID parameters and remove error constraint in followLine method
2025-11-28 to choose which pid to tune
2025-11-28 pin config of tofs fixed and grabber tof refactored to right tof
    [main.cpp]
2025-11-28 Refactor Robot class to include additional ToF sensor and update PID methods for single and double wall following
2025-11-28 Refactor ramp PID parameters and improve followRamp method for better speed adjustment
2025-11-30 Add CurrentSensor and Grabber classes with example usage
    - Implement CurrentSensor for current measurement and spike detection.
    - Create Grabber class to manage servo operations for grabbing and lifting.
    - Update ServoMotor class for improved initialization parameters.
    - Modify platformio.ini for compatibility with Arduino Uno.
    - Add example sketches for CurrentSensor and Grabber functionality.
2025-12-02 save colorsensor calibration to eeprom
2025-12-02 output enable in color sensor
2025-12-03 Refactor motor control and robot behavior
    - Updated Motor class to support separate PWM pins for forward and backward motion.
    - Modified Robot class to improve movement functions and PID control.
    - Enhanced MenuSystem with additional functionality for wall following and object detection.
    - Adjusted main setup to initialize motors and sensors with new configurations.
    - Cleaned up commented-out code and improved readability across multiple files.
2025-12-03 Refactor Grabber initialization and add liftBox method; update color sensor initialization in main
2025-12-04 calibrate colorsensor fix
2025-12-05 new calibration for color sensor
2025-12-06 Refactor: Rename digitalRead to readDigital and update references
    [arduino_mega_pinout.xlsx]
2025-12-06 Refactor: Update TOF sensor initialization and add goCellWithDetect method for enhanced box detection
2025-12-07 Refactor turn logic in Robot class; simplify _turnCore method and adjust PID parameters
2025-12-07 bool gyroMode
2025-12-07 Add MPU6050 integration and enhance movement logic with gyro support; update Junction and Robot classes
2026-02-28 Moved design files
    [Ball Bearim 1_V0.2.SLDPRT, Ball Bearim 2_V0.2.SLDPRT, Ball Bearim 3_V0.2.SLDPRT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]
